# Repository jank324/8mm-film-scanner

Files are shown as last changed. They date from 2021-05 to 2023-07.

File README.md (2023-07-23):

# 8mm Film Scanner

The _8mm Film Scanner_ is a project to build a scanner for digitising 8mm motion picture film in both the _Regular 8_ and _Super 8_ gauges by converting an old projector with the help of a [Raspberry Pi](https://www.raspberrypi.org) single board computer.

In this repository, I have collected all my materials on this project, including source code, information on the hardware and software design, instructions for using the software, a rundown of my scanning and editing workflow and many more.

You might also want to check out my [post about this scanner over on the *Kinograph* fourms](https://forums.kinograph.cc/t/8mm-film-scanner-my-build/2574).



### Table of contents

- [Introduction](#introduction)
- [Detailed technical description](#detailed-technical-description)
  - [Hardware design](#hardware-design)
    - [Projector conversion](#projector-conversion)
    - [Camera](#camera)
    - [Electrical systems and wiring](#electrical-systems-and-wiring)
    - [Base plate and case](#base-plate-and-case)
  - [Software design](#software-design)
    - [Scanning operations](#scanning-operations)
    - [Dashboard and other user experience](#dashboard-and-other-user-experience)
  - [Scanning workflow](#scanning-workflow)
  - [Cost](#cost)
  - [Future features and fixes](#future-features-and-fixes)
- [Run the software on your own scanner](#run-the-software-on-your-own-scanner)
  - [Installation](#installation)
  - [How to use](#how-to-use)
- [Contributing](#contributing)
- [Acknowledgements](#acknowledgements)

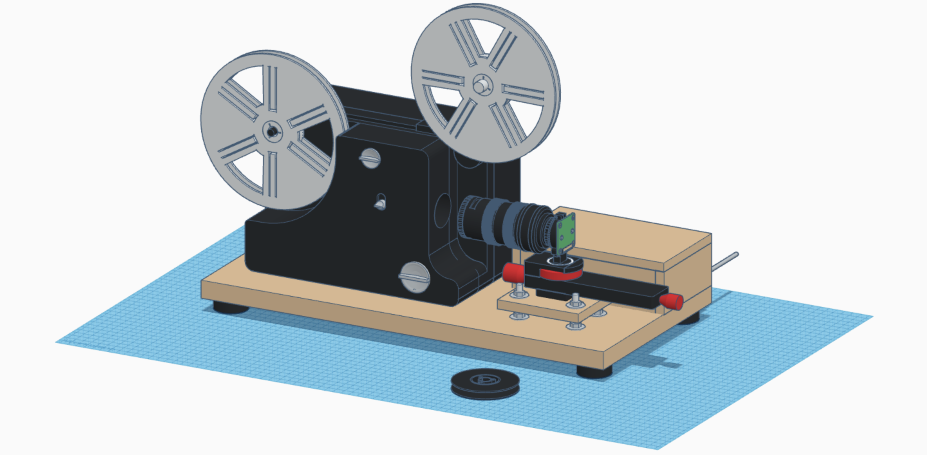
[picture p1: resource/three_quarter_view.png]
Three-quarter view render


## Introduction

I while ago, I found myself with over 800 rolls of 8mm film my grandfather had filmed throughout the 1960s, 70s and 80s. Having just digitised my grandparents' photo collection, naturally I wanted to know what was on these 8mm films and digitise them as well, so they would be safe from further deterioration and so we would actually watch them instead of always being too lazy to set up the projector.

The easiest way to get films like these digitised is the use of a digitisation service. But for the sheer amount of film I had, this would have cost me well over 10,000€ and with these services you never know whether you will actually receive a decent quality scan. The next option was to get out the old projector and use a video camera to record the films as they play. This is a perfectly valid option and super easy to do, but the resulting recordings usually suffer from image distortion, bad colours, a lack of sharpness and quite a bit of flicker. To do the true quality of these films justice, what was really needed was a frame-by-frame scanner that takes an image of every single frame of the film directly off of the film itself. You can actually buy these, but the ones available are either so expensive that they only make sense for professional users (e.g. scanners by [Filmfabriek](https://filmfabriek.nl)) or they leave a lot to be desired in terms of quality (like the famed [Wolverine](https://www.wolverinedata.com/products/MovieMaker_Pro)).

The solution is to build your own scanner, an idea that I got hooked on after finding a [video on the AACA Library's _Mike's Movie Machine_](https://www.youtube.com/watch?v=luGacxJMZI8), which is really just an incarnation of the absolutely amazing [_Kinograph_](https://www.kinograph.cc) project. The Kinograph project is accompanied by the [Kinograph forums](https://forums.kinograph.cc), quite possibly the best community on motion picture film scanning you will find on the internet, hosting invaluable information and some incredible projects built by talented and passionate people. On scanner build project in particular that I would like to point out as they key inspiration for this project is [the build by Scott Schiller](https://youtube.com/playlist?list=PLIACRGgedheWF4xr1zxiASZ1QqJUfloQ2), who also produced an awesome video series about his scanner and his scanning workflow.

In the following, you will find a detailed description of my _8mm Film Scanner_ as well as my scanning workflow, using a dual-gauge film projector and a [Raspberry Pi](https://www.raspberrypi.org) with a _HQ Camera_.

Some of the features of this scanner include:

- Dual gauge scanning of both _Regular 8_ and _Super 8_
- Up to 3K resolution (though 2K is recommended, 4K is possible with modifications)
- Scanning independent from a computer, allowing for unattended scans
- RAW scanning workflow
- Support for up two 120 m (400 feet) reels
- An easy-to-use web interface (with a mobile version as well as light and dark modes)
- Once-piece design that takes no time to set up or stow away

Below you find ...

- ... a photo of the scanner
  Photo of the scanner

- ... a screenshot of the scanner's web interface (light mode)
  Web interface in light mode

- ... a video of sample scans

  https://github.com/jank324/8mm-film-scanner/assets/17012833/1bc203a3-f0e7-4aa9-b80b-c313283cab2c

The rest of this README is intended as a documentation of every detail and lesson learned about my scanner. The goal here is to provide all the information and source code required to build another one.

## Detailed technical description

This section will go over technical details of the _8mm Film Scanner_. The goal is to document provide other (or even myself at some point in the future) with everything needed to rebuild the scanner without having to redo all the research I did.

### Hardware design

In this section, the hardware of the scanner is described. It will go over how the projector was converted to be a scanner, the camera sensor, lenses and mount, the electronics supplying power to and communication between the components as well as the base plate holding everything together.

#### Projector conversion

The scanner is built around a _Bolex 18-3 TC_ dual gauge film projector. There was no particular reason why I used this projector other than that I found a very cheap one sold as defective in the local ads. I never tested the electric components of the projector, but the film transport was in perfectly fine condition, which is all I cared about for this project.

There are some almost identical models to this one by Bolex and Eumig, including the Bolex 18-3 Duo, Eumig 610 D, Eumig 605 D, Eumig 614 D and Revue Lux 3003. So, if you would like to follow along with this build, the conversion should be almost the same for these models. Other projectors, however, will also be just fine and look fairly similar.

In order to convert the projector, I removed the power supply and the motor/fan assembly from the left side of the housing. In its place, I mounted an acrylic base plate to mount new components to. A photo of the baseplate with its components is shown below. For this particular projector, a tensioning arm for the main drive chain was originally mounted to the motor/fan assembly. This was simply remounted on the base plate. Furthermore, a [Nema 17 1.5 A 12 V stepper motor](https://www.amazon.de/gp/product/B07KZQ77VH/ref=ppx_yo_dt_b_search_asin_title?ie=UTF8&psc=1) was mounted using a right angle [mounting bracket](https://www.amazon.de/gp/product/B07CM3LZD1/ref=ppx_yo_dt_b_search_asin_title?ie=UTF8&psc=1) designed for NEMA 17 stepper motors. A pulley is mounted to the shaft of the stepper motor. This pulley should match the belt shape and size of the projector, but it is possible to get away with mixing v-belts and a pulley for round belts. I've chosen [this pulley](https://www.amazon.de/gp/product/B07C4R3PGV/ref=ppx_yo_dt_b_asin_title_o05_s00?ie=UTF8&psc=1). Pulley needs to be aligned with the pulley on the projector's main drive shaft (in my case also the aperture wheel). The stepper motor needs to be mounted at the same distance to the drive shaft pulley, such that it maintains the same tension on the drive belt as the original motor did. It might also make sense to replace the belt with a new one. These are readily available online by searching for the projector's name. In addition to the stepper motor assembly, a [KY-024 Hall effect sensor](https://www.amazon.de/gp/product/B089QK1CHR/ref=ppx_yo_dt_b_search_asin_title?ie=UTF8&psc=1) is mounted on the rear of the baseplate using a right-angle bracket. A small [5x1 mm Neodymium magnet](https://www.amazon.de/gp/product/B07T13H3R5/ref=ppx_yo_dt_b_search_asin_title?ie=UTF8&psc=1) is mounted to the core of the aperture wheel. The hall effect sensor and the magnet need to be lined up. They are used to detect that the scanner has advanced one frame. Parts of the electronics are also mounted to the base plate, either using double sided tape or screws as appropriate. They are further described in the [Electrical systems and wiring](#electrical-systems-and-wiring) section.

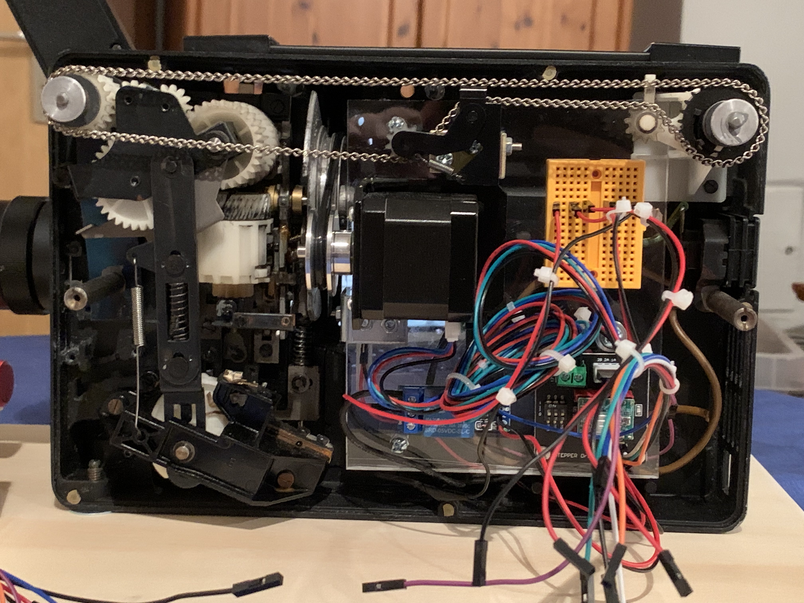
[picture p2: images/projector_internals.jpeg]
Projector internals


On the right side of the project, the original lens is remove. This allows the camera to take take photos of the film directly from the film gate. Furthermore, I removed a mask from the film gate in order to be able to capture a larger area of the original film frame. I did not drill out the film gate because I did not want to risk scratching the film, but this is certainly an option, if removing the mask does not reveal all of the frame. Neither removing the mask nor drilling out the gate is strictly required, but merely allows the scanner to capture more of the frame the would have been projected.

The original halogen bulb of the projector is replaced with an LED light bulb. Doing so is critical because the film and likely some of the components of the projector would overheat otherwise. Replacing the bulb with an LED very easy on this and many other models of projector, as MR16 LED bulbs can be mounted without any modifications. The bulb should be at least CRI 90+ and produce about 270 lm at an angle of 38°. I chose [this 3W bulb by _greenandco_](https://www.amazon.de/gp/product/B07F14F3N7/ref=ppx_yo_dt_b_search_asin_title?ie=UTF8&psc=1). Note that very similar 6.5 W _Philips Master expertcolor_ LED with with 420 lm turned out to be too bright in my earlier experiments. The colour temperature of the bulb should ideally be similar to the original halogen bulb, i.e. somewhere around 2700 K. In addition to mounting an LED bulb, the light of this bulb also needs to be further diffused. I used a 3mm sheet of white acrylic, specifically [_PLEXIGLAS LED white WH52 GT_](https://www.plexiglas.de/en/products/plexiglas/plexiglas-led). This specific type of acrylic by PLEXIGLAS is specifically designed to be colour-accurate for lighting applications and PLEXIGLAS themselves sell small samples for very little money. These samples are more than large enough (in fact I had to cut mine in half) for mounting in front of the MR16 bulb. Note the _WH52_ indicating the level of diffusion (and light attenutation) that work well with the LED bulb I chose. The acrylic is mounted to the front of the bulb mounting bracket using double sided tape as can be seen in the photo below.

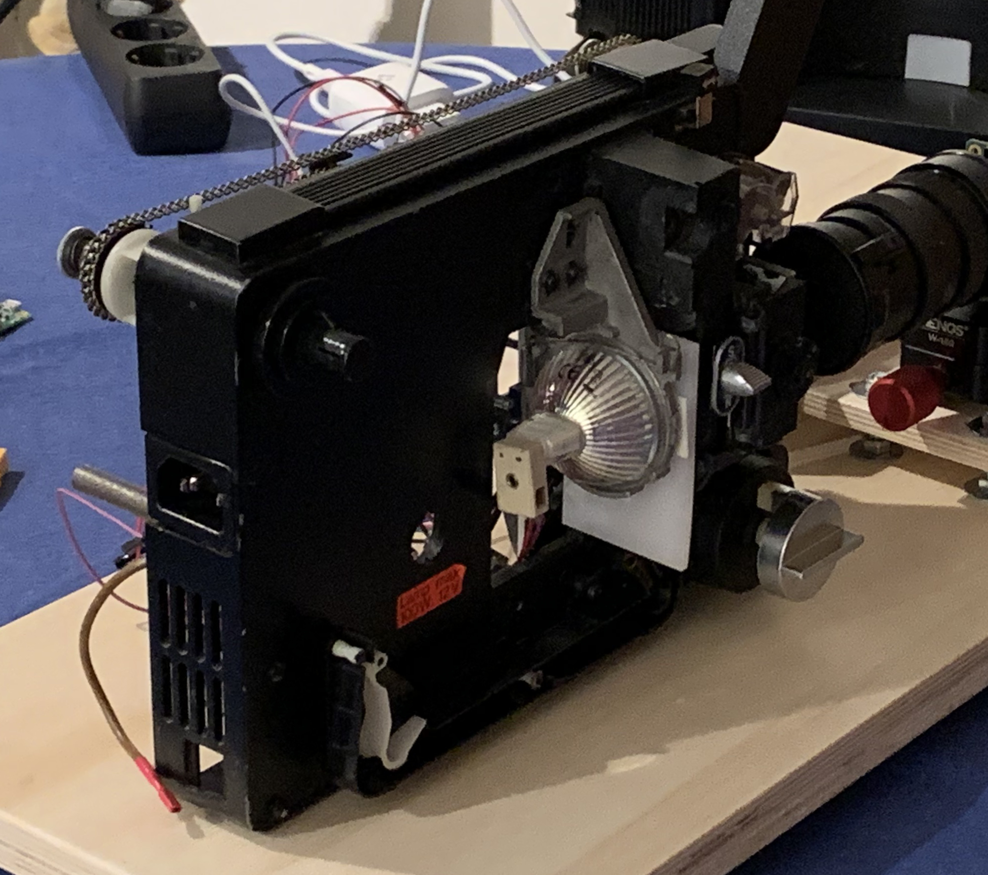
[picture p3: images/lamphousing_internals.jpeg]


#### Camera

The scanner uses the [_Raspberry Pi HQ Camera_](https://www.raspberrypi.com/products/raspberry-pi-high-quality-camera/) to capture the frames on the film. This model was chosen because it is easy to use with the Raspberry Pi, the image quality is more than adequate and the C-mount as well as its sensor size make it easy to adapt lenses and achieve the magnification required to have the small film frames fill the camera's image sensor.

The lens used is a _Schneider-Kreuznach Componon-S 50mm_ enlarger lens. Today, enlarger lenses are widely available on the used market. They well-suited to macro imaging applications and usually have a very flat image plane, helping us avoid focus vignetting. The Componon-S in particular is a very good quality model and a popular choice in the film scanning community, but other similar enlarger lenses are just as well suited.

The Componon-S has an M39 thread and therefore needs to be adapted to the camera's C-mount. It also needs to be mounted at some distance from the image sensor to achieve the enlargement required to make a Regular 8 or Super 8 frame fill the camera's sensor. As finding adapters directly from C-mount to M39 turned out to be rather difficult, I chose to adapt via M42-mount. This mount was widely used by Pentax in the 1960s and 70s, making adapters to other mounts as well as macro extension tubes very easy to find. The following components are used to adapt the enlarger lens to the HQ Camera (starting from the camera):

- C-mount to M42 adapter
- 19 mm M42 extension tube
- 26 mm M42 extension tube
- M42 to M39 adapter ring (screws into the inside of the M42 thread and is therefore not visible)

The picture below shows the final camera assembly. Note that the M42-to-M39 adapter is not visible as it screws into the inside of the extension tube's thread before the lens is screwed in.

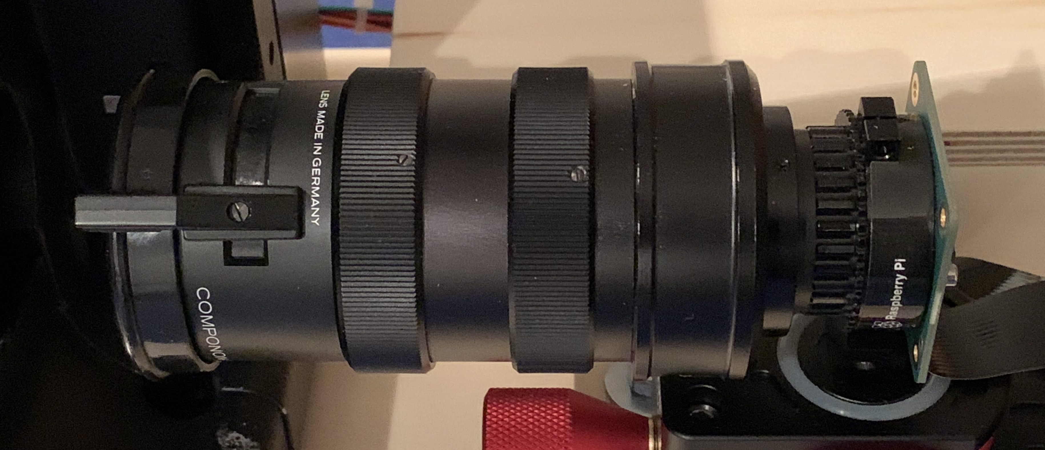
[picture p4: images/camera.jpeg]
Camera


Using the HQ Camera's tripod mount, the camera is mounted on a _MENGS W-160_ macro slider that can be used to adjust focus. The same macro slider can often be found under different brands. The macro slider itself is mounted to a wooden baseplate with a [3/8-16x1 screw with a hex head](https://www.amazon.de/gp/product/B07JGWWSFK/ref=ppx_yo_dt_b_search_asin_title?ie=UTF8&psc=1) that was shortened. Four M6x50mm screws with hex heads are used to mount the base plate to the main plate of the scanner. Using four pairs of nuts and washers, it is possible to adjust the height of the camera. The four wholes to mount the base plate are elongated in parallel to the film plane, allowing for horizontal adjustment of the camera position. More details and measurements of this camera mount can be found in the [Base plate and case](#base-plate-and-case) section.

The lens is always used at an aperture of f4.7. This was found to be the aperture at which the lens is by far the sharpest and lets in the correct amount of light for the rest of the camera setup.

The forward end of the lens is somewhere around 78 mm away from the film gate, but this has likely changed since as a result of focusing adjustments.

I have published [further studies on the camera setup on the Kinograph forums](https://forums.kinograph.cc/t/reverse-mounting-schneider-componon-s-50-mm-on-c-cs-mount/1767/8?u=jankaiser).

#### Electrical systems and wiring

Below you can see an overview of the scanner's electrical systems with red and black connections representing positive and negative power connections, and all other colours representing signal connections.

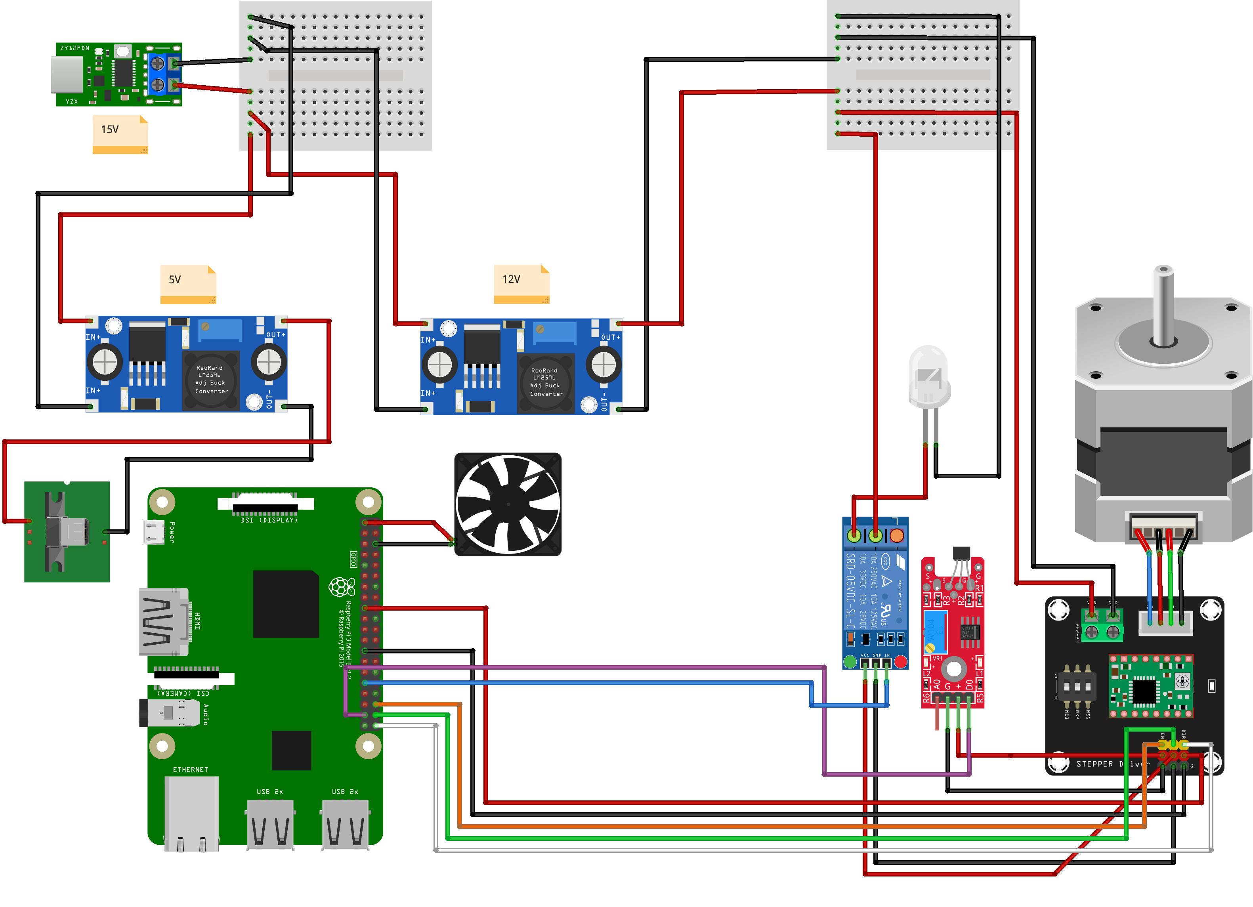
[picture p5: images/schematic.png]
Overview of electrical systems


The scanner is powered by a fairly standard [45W USB-C power supply](https://www.amazon.de/gp/product/B098P15D4N/ref=ppx_yo_dt_b_search_asin_title?ie=UTF8&psc=1). The power supply is connected via a USB-C cable with USB-C PD support to a [ZY12PDN USB-C PD trigger board](https://www.amazon.de/gp/product/B08FD6381L/ref=ppx_yo_dt_b_search_asin_title?ie=UTF8&psc=1). This board is capable of negotiating with the power supply that it should deliver power as well as the USB-C PD mode that is used. Different modes differ primarily in the delivered voltage. The trigger board can be configured via a button on the board to negotiate a particular voltage. In this particular case, the trigger board is configured to negotiate the 15V mode, though 20V would work just as well. Note that the power supply must support the mode. If the power supply does not support the mode the trigger board asks for, USB-C PD will fall back to 5V. At this voltage the scanner will not work, but 5V will not damage it either.

A pair of [LM2596S step down modules](https://www.amazon.de/gp/product/B07YWLCTLK/ref=ppx_yo_dt_b_search_asin_title?ie=UTF8&psc=1) are then used to step the 15V from the power supply down to 5V required by the Raspberry Pi and 12V for the stepper motor and the LED light. While it would be possible to connect the Pi to the step down converter directly using jumper wires on its GPIO pins, the Micro USB end of an old USB cable is used instead. This keeps the Pi's fuses in circuit and protects the Pi in case of a problem with the power supply.

The stepper motor is driven by an [A4988 stepper driver](https://www.amazon.de/gp/product/B07C2V9GWC/ref=ppx_yo_dt_b_search_asin_title?ie=UTF8&psc=1) that sits on a [very practical PCB](https://www.amazon.de/gp/product/B07RGJQFSX/ref=ppx_yo_dt_b_search_asin_title?ie=UTF8&psc=1) which makes it easier to mount and connect the driver. The Pi controls the stepper motor direction via its GPIO 21 pin (white), enables the stepper via its GPIO 16 pin (orange) and steps the motor via its GPIO 20 pin (green). Using the switches on the PCB, the driver is configured to run the stepper motor in full-step mode. Note that this PCB also has additional positive and ground supply pins which are used to make the Pi's 3.3V available in the projector housing due the the location of the Pi in the wooden case.

The LED light is controlled by the Pi using a KF-301 relay module that can switch the 12V supply to the light. The relay receives its logic power from the 3.3V supply of the Pi and is controlled via the Pi's GPIO 6 pin (blue). It is important that the relay is connected to the 3.3V supply and **NOT** the 5V supply, the the logic level is 3.3V and it will not trigger properly otherwise. The relay is connected to the LED light through through the original bulb's GU5.3 socket.

The hall effect sensor, too, is connected to the Pi's 3.3V rail through the stepper PCB. It's digital signal output is connected to the PI via the GPIO 26 pin (purple). A potentiometer on the hall effect sensor module allows for setting the threshold of the digital trigger. This setting will likely need adjusting to make the scanner work properly.

The Pi also supplies a small case fan from its 3.3V supply. The fan has proven critical in cooling the Pi inside its cases. A heatsink is also mounted on the Pi's SOC. All cooling components were purchased as part of a typical [Raspberry Pi cooling kit](https://www.amazon.de/gp/product/B07C2V9GWC/ref=ppx_yo_dt_b_search_asin_title?ie=UTF8&psc=1).

Two [mini breadboards](https://www.amazon.de/gp/product/B01M9CHKO4/ref=ppx_yo_dt_b_search_asin_title?ie=UTF8&psc=1) are used to help manage the wiring both inside the projector and the case containing the rest of the electronics.

#### Base plate and case

To make setting up the scanner and stowing it away as easy as possible, the entire system is mounted on a base plate. The base plate also provides housing for the electronics that did not fit into the projector's housing.

The entire base plate is built from 9 mm poplar plywood. For the main part of the base plate, two 9 mm sheets were glued together, giving the base a strength of 18 mm. The housing for the electronics is placed in the front left corner of the base plate. It is fully glued together. There are openings for the Raspberry Pi's ports and the power connector on its left side. A round hole on its rear side allows for wires to be passed through toward the projector housing. On the case's left side, three slits allow for cooling and a narrow slit is placed on the bottom for the camera's ribbon cable. The lid of the case is two sheets of plywood glued together, with the bottom sheet being smaller than the top one to allow the lid to sit firmly on the top of the case. For protection, all wooden parts of the base plate are painted using [edding 5200 semi gloss clear coat](https://www.edding-fachshop.de/edding-5200-Permanentspray-Klarlack-4-5200995-ar941.aspx), but other clear coats should do just fine. The image below provides dimensions for the base plate.

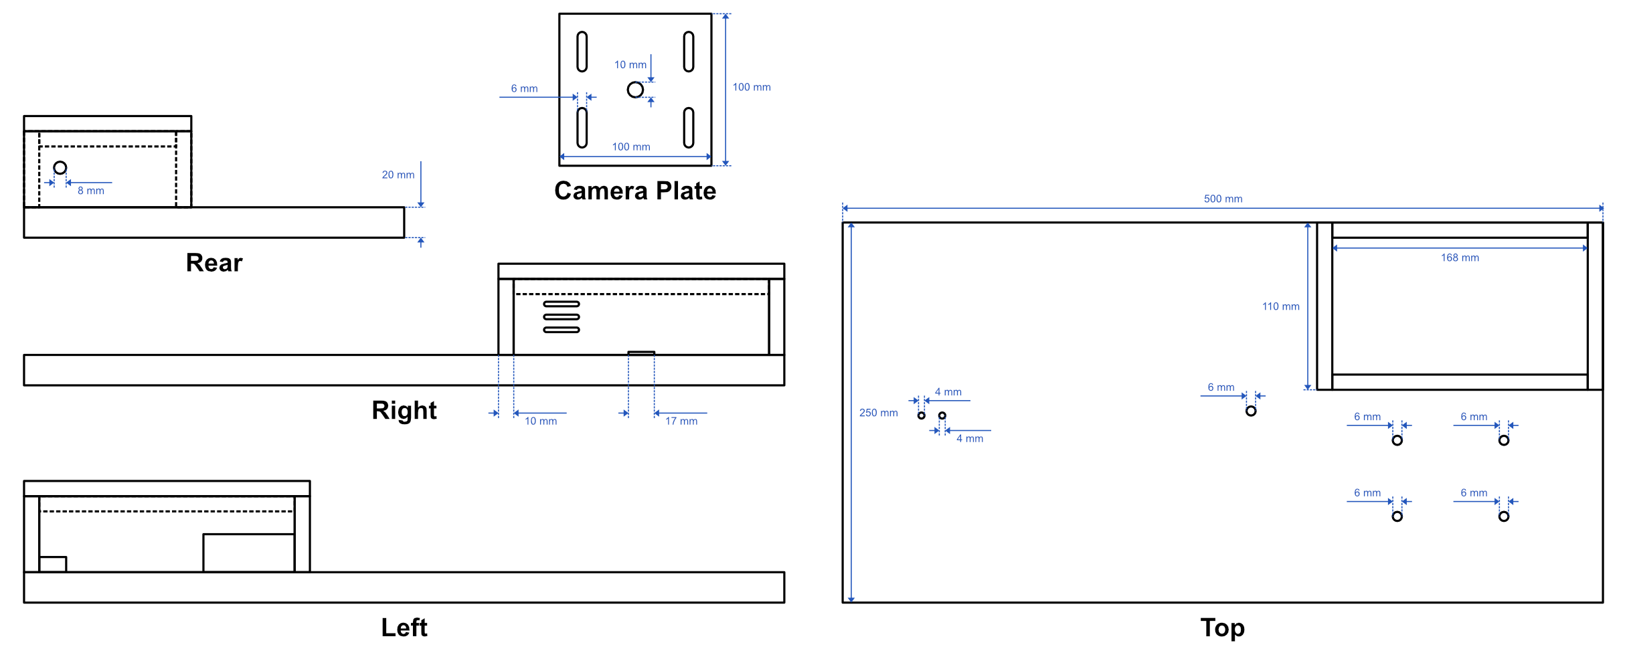
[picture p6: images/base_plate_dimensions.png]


Inside the electronics housing, all PCBs are mounted using double sided tape. The same applies to a small cooling fan mounted in the inside of the three cooling slits. This fan is strictly necessary to provide cooling to the Pi and the power supply components. I have found in tests, that with the fan and the cooling radiators installed on the Pi, the SOCs temperatures under load remain significantly lower than they do with the Pi out in the open air but without a cooling fan or radiator. The inside of the electronics housing is shown below.

Case internals

The projector is mounted using screws through holes. The screws are screwed through the base plate and into the holes that the projector's feet were originally screwed into. Note that this particular projector uses a special type of screw thread on the front that is 6mm in diameter and has two threads, each with twice the pitch of a standard M6 thread. I was unable to find buy a suitable screw for this, but the original foot is effectively a screw and worked just fine as such to mount the projector to the base plate. To mark the screw holes for the projector in the correct locations, a piece of paper was place on the bottom of the projector, the holes were traced and then transferred to the plywood. As the bottom of the projector is not at a perfect right angle relative to its sides and the film gate, washers were pushed under the higher side such that the projector stands mostly upright.

A camera mounting plate made from plywood is installed in the front left corner. It is further detailed in the [Camera](#camera) section.

### Software design

The software for this project consists of two parts: the film scanning logic taking care of film advance and image capture, and the user interface logic serving a web interface to simplify and streamline the interaction with the scanner.

#### Scanning operations

The scanning operations, including advancing the film and capturing frames, are handled by the `FilmScanner` class. Scanning is done by capturing the current frame, submitting it to a concurrent save method and then triggering the frame advance before repeating the process. To advance to the next frame, the stepper motor is ramped up and then run at a constant speed until the hall effect sensor was detected, at which point it is ramped down again. There is both a minimum time that has to pass before a completed frame advance may be detected as well as a timeout. If a timeout is detected before the hall effect sensor, the scanner will attempt to recover by reversing the advance mechanism until the hall effect sensor it detected and then reattempting the frame advance. Before submitting a frame for concurrent saving, the scanner might wait, if the previous frame has not finished saving yet. This prevents unsaved frames from piling up if the memory is slow for some reason.

The `pigpio` package is used to interface with the Hall effect sensor, the LED light and the stepper motor. The `picamerax` package is used to interface with the HQ camera.

The scanning code provides callbacks for various events, such as beginning and end of a scan, make it easy to implement various functions, e.g. the GUI or e-mail notifications, without the need to modify the actual scanning code.

#### Dashboard and other user experience

In order to make setting up and monitoring scans easier, the scanner provides a GUI. The goal was to make the scanner fully independent from other devices, such that a scan can be set up and then run fully unattended without even the need for a PC to be connected. To this end, a web interface was chosen. The web interface can be opened on any PC or even smartphone or tablet with a browser that is on the same network as the scanner, and it can be closed as soon as the scan is setup without interfering with the scan. Furthermore, the web interface can be reloaded at any time to check on the scan, again without interfering with the latter. Screenshots of both the desktop and mobile version of the web interface are shown below.

| Desktop web interface (dark mode) | Mobile web interface (dark mode) |
| :---: | :---: |
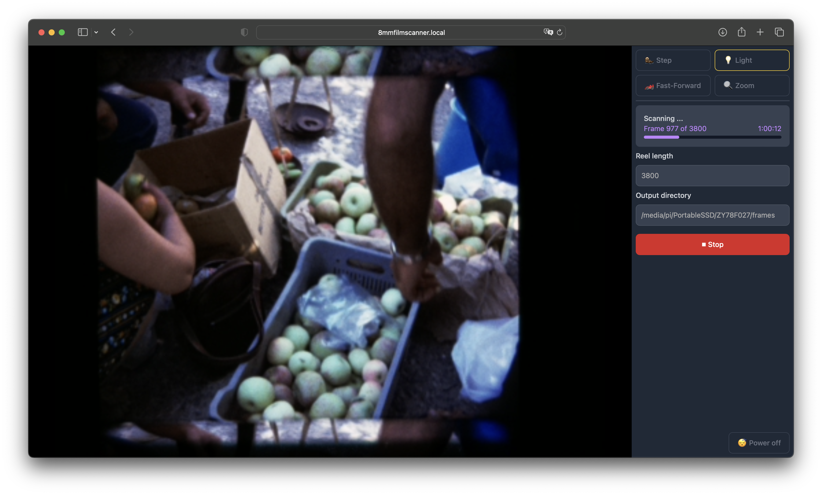
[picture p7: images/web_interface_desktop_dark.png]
Desktop web interface dark mode
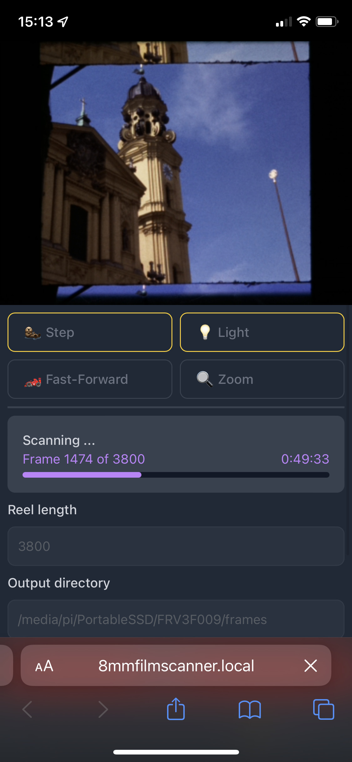
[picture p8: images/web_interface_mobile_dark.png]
Mobile web interface dark mode
|  |  |

The web interface is implemented in `server.py` using the _Flask_ package. A number of commands that can be sent to the scanner are implemented via different routes. The scanner also streams a live preview of the camera. During scanning, this preview is replaced with the most recently scanned frame.

The frontend of the web interface is implemented in Javascript as a [_React_](https://react.dev) app in the `frontend` directory. [_Tailwind CSS_](https://tailwindcss.com) was used for styling.

Automated e-mail notifications are implemented using a callback to the callbacks provided by the `FilmScanner` class. These are currently set up to send an e-mail notification when a scan has finished or was aborted because of some error. Note that this requires the scanner to have either its own e-mail account or access to the user's e-mail account.

### Scanning workflow

In this section I would like to briefly go over my current scanning workflow to illustrate how the scanner may be used to produce archivable digital copies of 8mm film reels. Note that this is what my workflow looks like right now and likely to change and evolve over time. It also certainly is not the only way to do it and there probably are better ways to get the results you are looking for.

Before starting to scan any of my film, I actually started by creating a list of all the film I have, giving every film a unique ID so I can identify them later. This allows me to easily track the progress of my scanning project over a long period of time and see which reels I have already scanning or what stage of post-processing I last left them in. Based on the IDs, I maintain a spreadsheet with various information on each reel. This includes their current status, which can be any one of _not digitised_, _old digitisation_, _in progress_, _scanned_ and _finalised_, where _old digitisation_ refers to a reel digitised with an inferior method many years ago and _finalised_ means that a reel has been into a larger film project (for example of all reels from a holiday). Further, the spreadsheet contains information on where to find the physical reel, the type of film, its length and what larger project the reel belongs to. In my particular case, many of the reels were actually labeled with detailed information on their contents. I have created a text document that with typed copies of these labels and the corresponding reel ID. A screenshot of the spreadsheet is shown below.

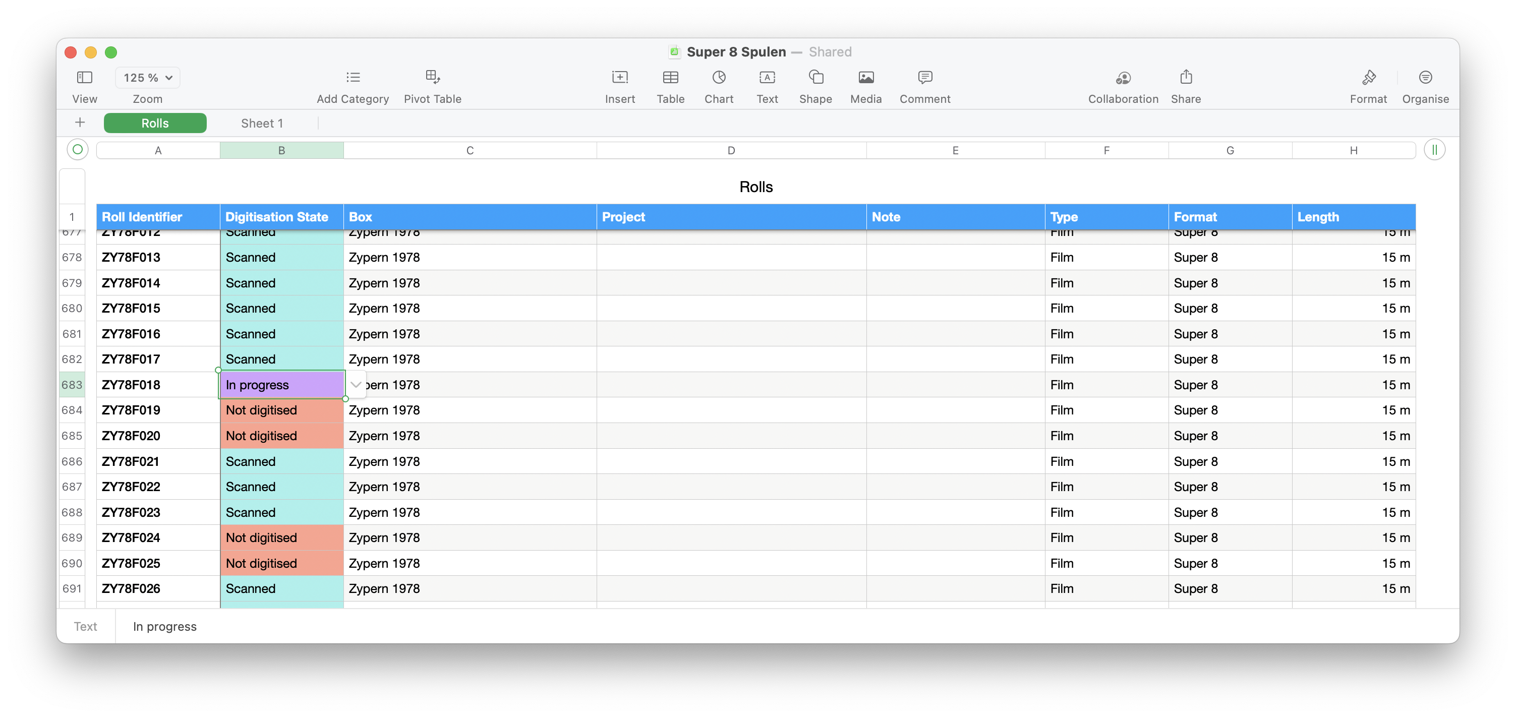
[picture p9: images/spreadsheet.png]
Spreadsheet


When it is time to scan a particular reel, I start by physically cleaning the film. To do this, I put the film on a film editing viewer. Then I put a few drops of [TETENAL Graphic Arts Film Cleaner](https://www.fotoimpex.com/darkroom/tetenal-graphic-arts-film-cleaner-1-liter.html) onto a lint-free cloth and spool the film onto another reel while grabbing the film with the soaked piece of cloth. It is advisable to swap the spot on the cloth every couple of meters and put on new cleaning solution as to avoid scratching the film with the dirt that came off it. Once the film is completely wound over, I wind it back onto its original reel. Note that I only attach the end of the film to the original reel very loosely so it comes off the reel easily when scanning. For your average Super 8 reel this is easiest done by not putting the film into the "claw" that is supposed to hold it, but to gently place it in the slit that usually allows you the see how full the reel is. Then just wind and the film will stay in place.

I then thread the film onto the scanner and fast-forward to the first frame that is fully visible. I use this frame to focus the camera onto the film grain. The _Zoom_ view offered by the web interface is very useful for the final focus adjustment. You might need to focus back and forth a little bit, until **the grain** appears as sharp as it gets.

For the number of frames to scan, I usually estimate the number of frames on the reel based on its length and the pitch of the film type, and then add ca. 5% to be sure to capture the entire film in one go. For example, for a 15 m (50 feet) reel, I capture 3800 frames, while the reel usually actually has around 3600 frames.

Rather than saving the scan on the Pi's SD card, I connect an external SSD via USB. It turns out this is significantly faster than using the SD card, so much so that with the SD card, the scan may be slowed down waiting for frames to save, which does not happen at all when using an external SSD. Note that I think for its speed, it is important to choose an SSD over a hard drive here. The path I select is `/media/pi/*path-to-ssd*/*rheel-id*/frames`.

Once the scan (or multiple scans) is done, I shut down the scanner and connect the SSD to my computer. At this stage I usually like to delete the empty frames from the end of the reel to save memory and processing time in the next steps. The Pi captures images, but only attaches the raw bayer data to JPG files. Therefore, the next step is to use the `dngconverter.py` script to convert the images to `.dng` files. Note that this specifically requires version `3.4.7` of the `pidng` package. The script provides a `--delete` option to automatically delete the original JPG files once they have been converted, but I prefer to do this manually once I know the conversion was successful. The converted DNG files may appear green. This is not a problem!

The next step is to import all the images into [_Adobe Lightroom_](https://lightroom.adobe.com). Here, we correct the white balance and the exposure, and crop into the frames, making sure to include the whole frame, not just a 4:3 crop of it. Some film stocks have changed colour or faded over time. They might required a colour correction as well. Luckily, the very common Kodachrome film stock usually retains its colours excellently. Use Lightroom's _Copy Develop Settings_ feature to make sure the settings are consistent for all frames on the reel (or at the very minimum the in the scene).

The `Super 8 Base (Kodachrome 1978).xmp` file provides a Lightroom preset that I always start from. It was tuned on unfaded Kodachrome stock that seems to have retained its colour just fine (it matches Kodak Ektachrome from 2022). This preset does three things: It matches the white balance to the light source, lifts the exposure to a be correct for a properly exposed film and reduces the contrast by lifting the shadows and lowering the highlights. The white balance was taken from a completely white and slightly underexposed photo of the film gate. Note that it does not perfectly match the advertised temperature of the LED, this is fine. The exposure is corrected in Lightroom instead of simply exposing one stop brighter in-camera to prevent highlights from blowing out. Pulling in the shadows and the highlights accounts for the naturally contrasty nature for positive film stocks and Kodachrome in particular.

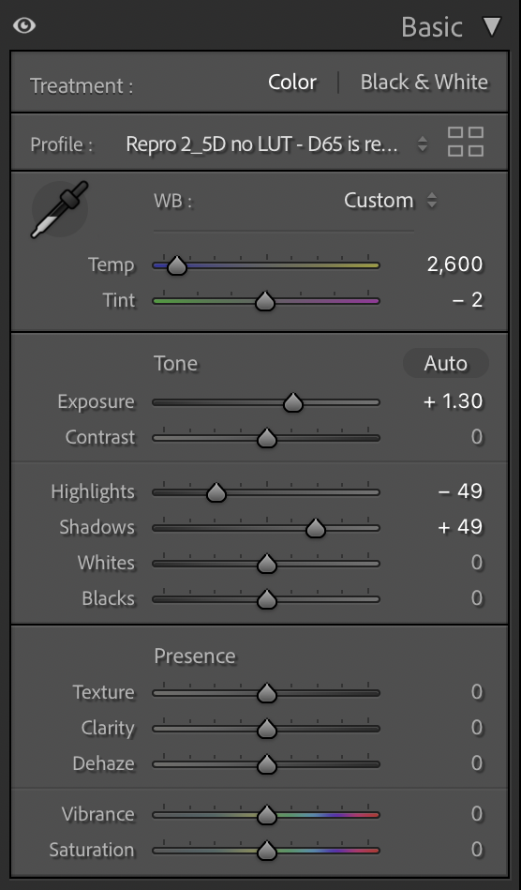
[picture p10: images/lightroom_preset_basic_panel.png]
Basic panel for the provided base Lightroom preset


While the provided exposure correction should be just fine for properly exposed scenes, you might encounter underexposed scenes in particular. Here it might make sense to pull up the _Exposure_ slider, but values of more than 2.9 usually don't reveal any more image details. Note that this is not a limitation of the image files, but of the film itself, as experiments with longer exposure times have shown. Next, the frames are exported as TIFF files. I choose 8 bit TIFFs, as the frames are already (mostly) exposure- and colour-corrected. I also turn off compression as these are only temporary files and doing so significantly reduces export times. I like to export to an `lr_export` directory right next to the original `frames` directory.

Once the export has finished, I use _Apple Compressor_ to render a video file from the exported images. Choose the little plus icon at the bottom of the Compressor window, click _Add Image Sequence_, select the `lr_export` directory with the exported frames in it and make sure to choose _Manually to_ with the correct frame rate for your film gauge (16 fps for Regular 8 and 18 fps for Super 8). I export to _Apple ProRes 422_ to retain quality in an intermediate format. In addition, I name my output file `*reel-id*_lr_export.mov` and save it in the same directory as the `frames` and `lr_export` directories.

At this point I check the exported video file, primarily because I'm excited to see the film for the first time, but also to check for issues that might warrant a second scan before I move on.

The next step is to fix defects and remove the gate weave from the footage in my video editing software. I use _Final Cut Pro_.

**Note:** While Final Cut doesn’t officially support 18 fps projects, with a little workaround it will handle custom frame rates easily:

1.  Create a new empty project make sure it already has the correct resolution and colour space set. You will not be able to change it later.
2.  With the project selected, go to _File_ → _Export XML…_ and save the `.xml` file somewhere.
3.  Open the `.xml` file and find all the `frameDuration` fields. Change them to match your desired frame rate in the format that they are currently in. A screenshot below shows an example changed to 16 fps below. Don’t forget to save the file.
4.  Now, go back into Final Cut. Select _File_ → _Import_ → _XML_ and select the `.xml` file.

You should now have a project that correctly shows that it is 16 fps (or whatever you selected). If you want to avoid having to redo this process all the time, you can simply duplicate the project when you need a new one.

**A little trick here:** Duplicating with the keyboard shortcut _cmd+D_ works even when the context menu item is greyed out. Only Apple know why 🤔.

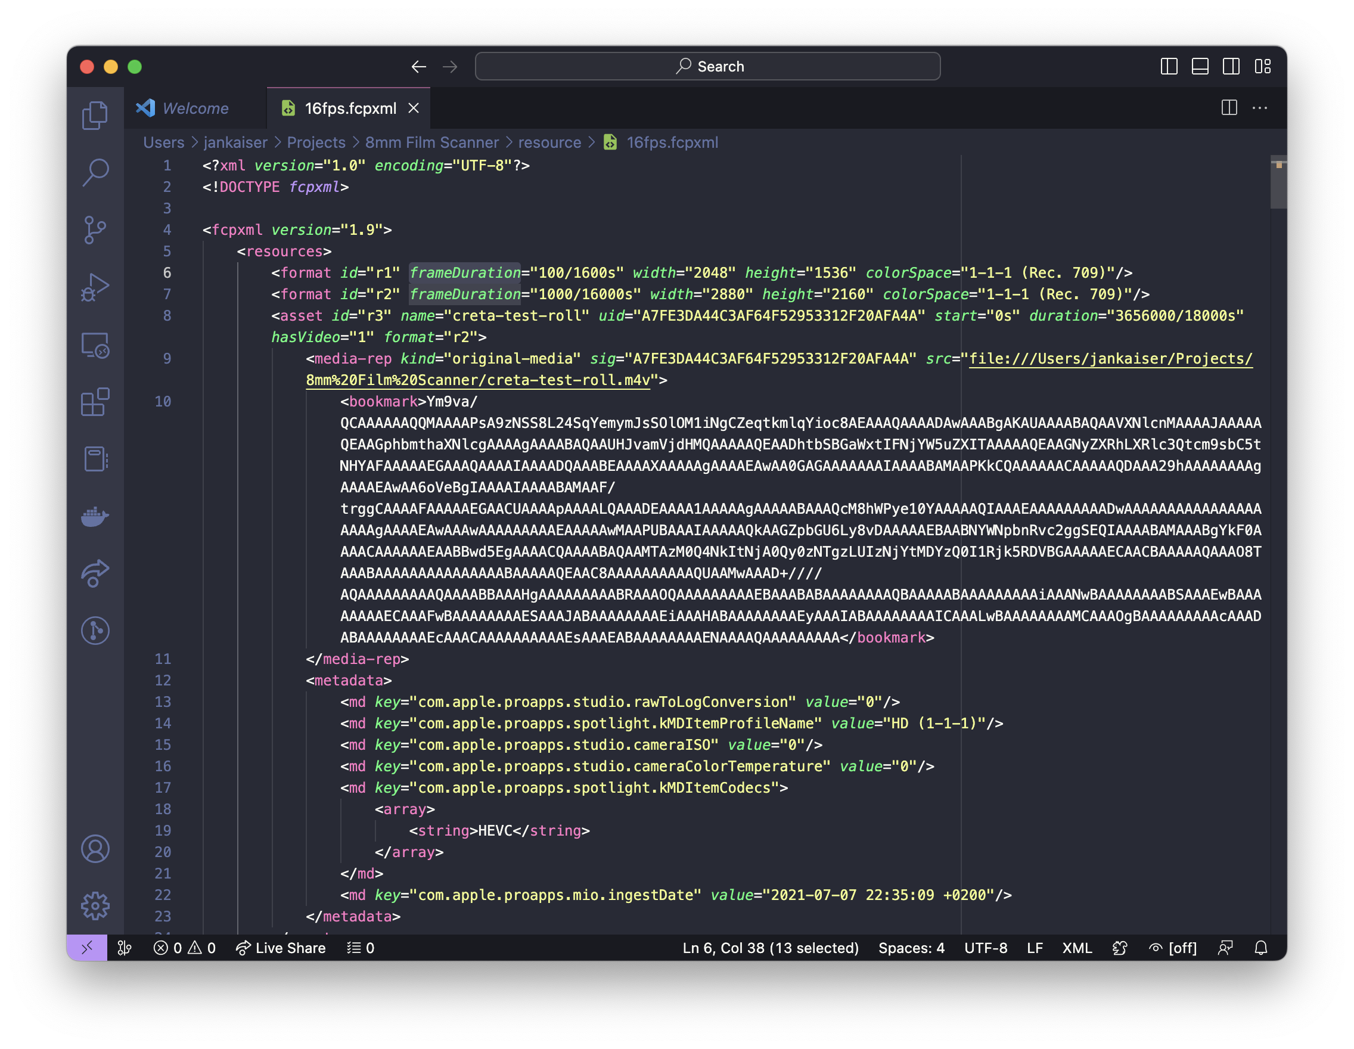
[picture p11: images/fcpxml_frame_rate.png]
Screenshot of a 16 fps .fcpxml file


After importing the clip, I first crop it to the correct aspect ratio by selecting _Spatial Conform_ -> _Type_ -> _Fit_ for the whole clip. Then I go through the clip from beginning to end and cut it at each scene change. Sometimes in analog film, frames between scene changes at overexposed or have light leaks. I like to remove these frames. I then stabilise each scene using the _SmoothCam_ method. To make sure I'm only removing the gate weave but retaining original camera movement as much as possible, I turn the _Rotation Smooth_ and _Scale Smooth_ settings all the way to 0.0. The _Translation Smooth_ setting is set to 0.33. Note that for any lower setting, Final Cut will not perform any stabilisation. In some scenes (for example when shot from a driving car) the natural shakiness of the footage overpowers the gate weave. In these cases, I will not stabilise the clip, because doing so would look over-processed and crop in too much into the original footage. Sometimes clips seems table, but Final Cut still chooses to crop in a lot. In these cases it might help to remove just a few frames from either end of the clip. This step of the process is also the right time to remove scenes with those from other scans of the same reel, if there were defects like black frames, doubled frames or large static pieces of dust in your scan.

Once all of this is done, I will export the clip to _Apple ProRes 422_ to `*reel-id* fixed and stabilised` and reimport it to Final Cut. This is done to reduce processing times in the next step.

For the next step, I create a new project in Final Cut and add two copies of the reel stacked on top of each other. I leave the top clip untouched and apply the [_Neat Video_](https://www.neatvideo.com) filter to the bottom one. In Neat Video, I deactivate the _Spatial Filter_. The _Temporal Filter_ is left activated and setup as shown below. These settings make sure to retain the grain but remove the dust. In an ideal world, I would just apply this filter to the entire clip. Unfortunately, this filter tends to produces quite unsightly artefacts from time to time. Therefore, I will go through the clip and deactivate sections of the unfiltered top clip only where there is a disturbing piece of dust, such that the bottom clip with the dust removed is visible for those frames. Sometimes is makes sense to only show part of a Neat Video frame, if there are artefacts in the rest of it. I find that the _Crop_ settings are usually the most convenient way to achieve this. My goal here is not to remove all the dust, but only to remove the dust that distracts from the viewing experience. Ideally the film would look like a very clean film would have looked in its day, not entirely free of dust, but not visibly dirty either. I achieve this by watching the film once, and removing all the dust that is clearly obvious. I then watch it again, preferably in full screen, and check if any such dust remains.

| Final Cut Pro setup for dust removal | Neat Video dust removal settings |
| :---: | :---: |
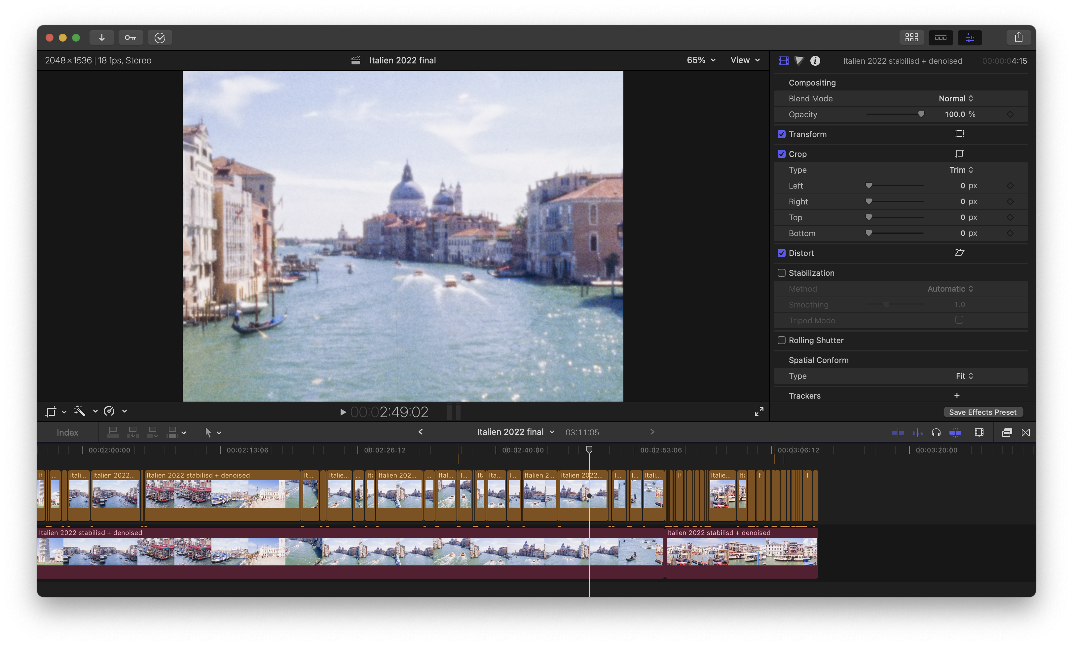
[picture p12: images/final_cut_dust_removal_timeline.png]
Final cut setup for dust removal
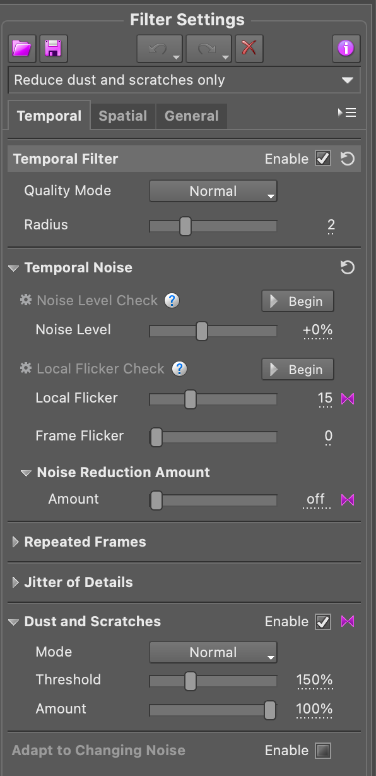
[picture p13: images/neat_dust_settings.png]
Neat Video dust removal settings
|  |  |

At last, I export the final clip as `*reel-id* final`. If the reel is part of a larger project, for example from a holiday, I will combine these final video files into a Final Cut project, once all reels have been scanned.

### Cost

Below is a table of all the items I used to build this scanner. Some of these I've already had, either because I bought them for an earlier project or because I was given them for some other reason. All prices are what I have actually paid or what I think they would have cost me if they were given to me. If I had to pay for shipping, this is included in the price. If I had to by multiple of the same item, even though I only needed one, I'm giving the price for the whole set. Your own milage may vary of course.

| Item | Price |
| :--- | ---: |
| Raspberry Pi 3B+ | 42.00€ |
| Micro SD card 32GB | 6.88€ |
| Jumper cables | 11.78€ |
| LED MR16 3W | 5.99€ |
| Relay | 3.99€ |
| Stepper Motor 1.5A | 10.99€ |
| Hall effect sensor KY-024 | 4.79€ |
| Neodymium magnets (100 pieces) | 6.99€ |
| A4988 stepper driver(s) | 7.49€ |
| Stepper driver parent PCB | 6.99€ |
| Stepper motor mount | 6.97€ |
| Belt pulley | 11.16€ |
| 50x25x6 mm acrylic sheet | 13.39€ |
| Raspberry Pi HQ camera | 59.78€ |
| Macro slider | 32.89€ |
| Screws | - |
| Bolex projector | 10.00€ |
| M42 to C-mount adapter | 39.90€ |
| M42 to M39 adapter | 7.26€ |
| Pentax extension tubes (3 pieces) | - |
| Schneider Componon-S 50mm enlarger lens | 64.99€ |
| 45W USB-C power supply (+ USB-C power cable) | 29.99€ |
| ZY12PDN USB-C PD trigger board | 12.99€ |
| Mini bread boards | 7.99€ |
| Poplar plywood 120x160x0.8 cm | 14.99€ |
| 38x15 mm rubber feet (4 pieces) | 4.99€ |
| 3/8-16x1 screw(s) | 6.99€ |
| PLEXIGLAS LED white WH52 GT sample | 3.00€ |
| Raspberry Pi cooling kit | 6.49€ |
| 50 cm Raspberry Pi camera ribbon cable | 7.99€ |
| Old micro USB cable | - |
| LM2596S step down modules (3 pieces) | 7.49€ |
| **Total** | **549.63€** |

### Current issues, future features and fixes

While the scanner has successfully scanned well over 50 reels over the past year already, there for remain a number of things that are not quite perfect just yet. I hope to fix these some day, but well all know that nothing survives as long as a temporary solution.

- **Dust removal workflow:** The dust removal as it is right now delivers excellent results, but it remains a lot of work. On a good day, I can currently finish the dust removal on one 15 m reel (just over 3 min) in 3-4 hours. At hundreds of reels to scan that is a very long time. Ideally, I would like a fully automatic solution. While Neat Video is great, letting it fully do a reel without supervision does not give satisfying results. In the future, I would like to explore a neural network-based solution, similar to already existing solutions for video restoration, but less heavy-handed.
- **Unreliable frame advance:** Most of the time the frame advance works just fine, but every 5k - 10k frames, it either produces a black frame, a doubled frame or a frame that is partially dark. This caused by the scanner not advancing fully, either because the Hall effect sensor was missed or because the belt connecting the stepper motor to the projector's mechanism slipped at the point where the mechanism has the most resistance. Unfortunately, because there is only this one sensor, the scanner cannot detect which of the two has happened (both have happened before, but now I suspect mostly the slipping). The problem is also difficult to debug due to it occurring so rarely, yet it happens often enough to be at least a little annoying. Possible solutions include:
  - Switching to a more reliable photo sensor. The Hall effect sensor seems to be not perfectly reliable due to its proximity to the stepper motor.
  - Adding a second sensor. This would allow the Pi to detect what has happened and recover it reliably if possible. To mount it, I would prefer to swap the base plate in the projector for a 3D-printed one that makes all components easier to mount.
  - Relubricating the projector's mechanisms. The projector's mechanisms may have more resistance than they should have. Adding new lubrication could fix this, but so far I have not dared to disassemble the mechanism to do this.
  - Ensuring proper belt tension on the drive belt. I have eyeballed the belt tension when installing the stepper motor, to be similar to the original motor. A slipping belt may be fixed by doing this properly. This is, however, outside of the scope of my personal expertise.
- **Crashing live preview:** Sometimes the live preview goes black or freezes. This is caused by the preview thread crashing. It is easily fixed by rebooting the scanner and therefore has not been annoying enough for me to fix yet. It, too, is difficult to debug as it only happens sporadically.
- **Lose PCB mounts:** All components in the Raspberry Pi case on the base plate are mounted using double sided tape. This is too lose, especially for the Pi and the USB-C PD trigger board, because they move a lot when plugging things in our pulling them out. The trigger board has actually come lose since I've mounted it. I would like to 3D-print a mounting rack that screws into the wood and holds all the components in the case firmly.
- **Web interface camera settings:** Adding camera settings to the web interface would be nice. I have not found the need for that yet, though, because all film stocks I have scanned so far worked with the same fixed exposure. This is actually to be expected with properly exposed films. Over- and underexposed films are easily fixed thanks to scanning in RAW format.

## Run the software on your own scanner

You are welcome to run this software or modified versions of it on your own scanner. A prerequisite is that the hardware is setup in roughly the same way (though it does not need to be based on a projector). You will need to make sure that the GPIO connections are either on the same pins as my scanner or that you change the code according to your connections.

These instructions may be incomplete. Furthermore, they have not been fully tested as I only have a single scanner. Please feel free to create an Issue for any questions you might have or problems you might find.

Start by cloning the repository (`Desktop`)

```sh
git clone https://github.com/jank324/8mm-film-scanner.git
```

and install the required Python packages.

```sh
sudo python3 -m pip install -r requirements.txt
```

Then install _npm_

`cd` to `frontend` directory.

```sh
cd frontend
```

and its required packages.

```sh
npm install
```

Continue to build the frontend via

```sh
npm run build
```

then `cd` back to the project root (`..`) where you can start the server by running

```sh
sudo python3 server.py
```

You probably want to run the server on boot of the Pi, so the scanner is ready to scan within seconds of you turning it on and without the need for you to start anything manually. To this end, this repository provides a _systemd_ service `8mmfilmscanner.service` that runs the 8mm Film Scanner's server on boot. To set up the service, copy the `.service` file to `/etc/systemd/system` by running

```bash
sudo cp 8mmfilmscanner.service /etc/systemd/system/
```

and then enable it via

```bash
systemctl enable 8mmfilmscanner
```

In order to send email notifications on finished scans, create a mail account of your choice or use your personal account. Create a file `notification_config.yaml` in the project root directory and fill in the following with the details of your mail account and the mail address you want e-mails to be sent to.

```yaml
user: scanners@mail.com # Address of the scanner's account
password: scanners-password-123 # Password of the scanner's account
to: your@mail.com # Address notifications are sent to (presumably your own)
```

Please remember to **NEVER** commit `notification_config.yaml` as it contains the password to the scanner's mail account which should remain secret. Under normal circumstances, this repository's `.gitignore` should already take care of this.

# Contributing

You are welcome to contribute to this project. If you find any issues, you may create a corresponding Issue here on GitHub. Even better, if you fixed something, you may create a Pull Request.

# Acknowledgements

First and foremost I would like to acknowledge Matthew Aepler and his [Kinograph forums](https://forums.kinograph.cc). The forums have been an invaluable resource for this project and are one of the best resources on motion picture film scanning out there. I would also like to acknowledge everyone who has contributed to the forums and thereby to this any many other projects. Furthermore, I would like to acknowledge [Scott Schiller and his scanner build](https://youtube.com/playlist?list=PLIACRGgedheWF4xr1zxiASZ1QqJUfloQ2), which have been a major inspiration for the direction of this scanner build project.

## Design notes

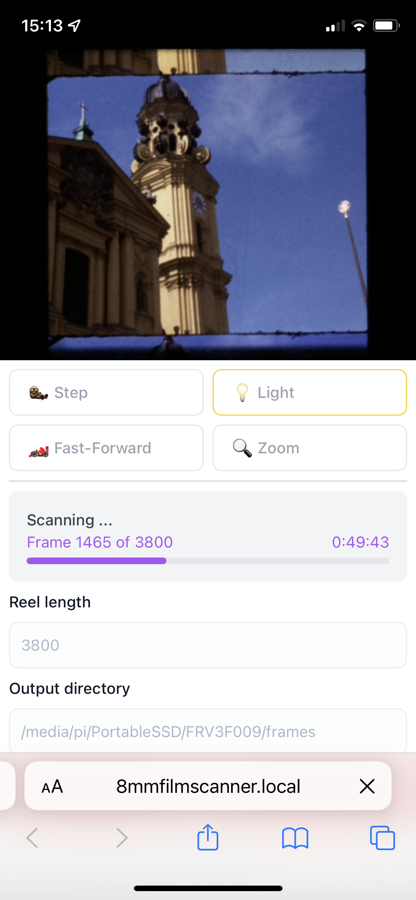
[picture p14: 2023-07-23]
images/web_interface_mobile_light.png

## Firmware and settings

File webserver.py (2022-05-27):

from flask import Flask, Response, request
from flask_cors import CORS

from filmscanner import FilmScanner
from notification import MailCallback
from utils import (
    AdvanceToggleCallback,
    FastForwardToggleCallback,
    LightToggleCallback,
    ScanControlsCallback,
    ZoomToggleCallback
)


app = Flask(__name__)
cors = CORS(app)

advance_toggle_callback = AdvanceToggleCallback()
fast_forward_toggle_callback = FastForwardToggleCallback()
light_toggle_callback = LightToggleCallback()
mail_callback = MailCallback()
scan_controls_callback = ScanControlsCallback()
zoom_toggle_callback = ZoomToggleCallback()

scanner = FilmScanner(
    callback=[
        advance_toggle_callback,
        light_toggle_callback,
        fast_forward_toggle_callback,
        mail_callback,
        scan_controls_callback,
        zoom_toggle_callback
    ]
)
scanner.camera.resolution = (800, 600)


@app.route("/advance", methods=("GET","POST"))
def advance():
    if request.method == "GET":
        return {
            "is_active": scanner.is_advancing and not (scanner.is_fast_forwarding or scanner.is_scanning),
            "is_enabled": not any([
                scanner.is_advancing,
                scanner.is_fast_forwarding,
                scanner.is_scanning
            ])
        }
    elif request.method == "POST":
        scanner.advance()
        return "", 204
    return "", 400


@app.route("/advance-stream")
def advance_stream():
    return Response(advance_toggle_callback.subscribe_to_sse(), mimetype="text/event-stream")


@app.route("/dismiss", methods=("POST",))
def dismiss():
    scanner.last_scan_end_info = "dismissed"
    return "", 204


@app.route("/fastforward", methods=("GET","POST"))
def fast_forward():
    if request.method == "GET":
        return {
            "is_active": scanner.is_fast_forwarding,
            "is_enabled": not (scanner.is_advancing or scanner.is_scanning)
        }
    elif request.method == "POST":
        if not scanner.is_fast_forwarding:
            scanner.fast_forward()
        else:
            scanner.scan_stop_requested = True
        return "", 204
    return "", 400


@app.route("/fastforward-stream")
def fast_forward_stream():
    return Response(fast_forward_toggle_callback.subscribe_to_sse(), mimetype="text/event-stream")


@app.route("/focuszoom", methods=("GET","POST"))
def toggle_focus_zoom():
    if request.method == "GET":
        return {
            "is_active": scanner.is_zoomed,
            "is_enabled": not scanner.is_scanning
        }
    elif request.method == "POST":
        scanner.live_view_zoom_toggle_requested = True
        return "", 204
    return "", 400


@app.route("/focuszoom-stream")
def focuszoom_stream():
    return Response(zoom_toggle_callback.subscribe_to_sse(), mimetype="text/event-stream")


@app.route("/light", methods=("GET","POST"))
def toggle_light():
    if request.method == "GET":
        return {
            "is_active": scanner.is_light_on,
            "is_enabled": not scanner.is_scanning
        }
    elif request.method == "POST":
        if not scanner.is_scanning:
            scanner.toggle_light()
        return "", 204
    return "", 400


@app.route("/light-stream")
def light_stream():
    return Response(light_toggle_callback.subscribe_to_sse(), mimetype="text/event-stream")


@app.route("/poweroff", methods=("POST",))
def poweroff():
    scanner.poweroff()
    return "", 204


@app.route("/preview")
def preview():
    def generate():
        for frame in scanner.preview():
            yield b"--frame\r\n" + b"ContentType: image/jpeg\r\n\r\n" + frame + b"\r\n\r\n" 
    return app.response_class(generate(), mimetype="multipart/x-mixed-replace; boundry=frame")


@app.route("/scan", methods=("GET","POST"))
def scan():
    if request.method == "GET":
        return {
            "is_scanning": scanner.is_scanning,
            "output_directory": scanner.output_directory,
            "n_frames": scanner.n_frames,
            "current_frame_index": scanner.current_frame_index if scanner.is_scanning else 0,
            "last_scan_end_info": scanner.last_scan_end_info,
            "time_remaining": scan_controls_callback.str_time_remaining
        }
    elif request.method == "POST":
        if not scanner.is_scanning:
            scanner.start_scan(
                output_directory=request.get_json()["output_directory"],
                n_frames=int(request.get_json()["n_frames"])
            )
        else:
            scanner.stop_scan()
        return "", 204
    return "", 400


@app.route("/scan-stream")
def scan_stream():
    return Response(scan_controls_callback.subscribe_to_sse(), mimetype="text/event-stream")


if __name__ == "__main__":
    app.run(host="0.0.0.0", debug=False)

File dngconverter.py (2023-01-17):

import argparse
from concurrent.futures import ProcessPoolExecutor, as_completed
from pathlib import Path

from pidng.core import RPICAM2DNG
from tqdm import tqdm


def bayerjpg2dng(jpg_path: Path, delete: bool = False) -> None:
    """
    Convert a the file at `jpg_path` to a `.dng` file. Deletes the old file if `delete`
    is set to `True`.
    """
    d = RPICAM2DNG()
    d.convert(str(jpg_path))

    dng_path = jpg_path.with_suffix(".dng")
    validate_file(dng_path, min_bytes=int(1e6))

    if delete:
        jpg_path.unlink()


def validate_file(path: Path, min_bytes: int = 1) -> None:
    """Check if file exists and has a file size larger than `min_bytes`."""
    is_valid = path.is_file() and path.stat().st_size > min_bytes
    if not is_valid:
        raise InvalidFileException(path)


class InvalidFileException(Exception):
    """Exception raised when a file was found to be invalid."""

    def __init__(self, filepath: Path) -> None:
        super().__init__(f'File "{filepath}" is invalid.')


def parse_arguments() -> argparse.Namespace:
    """
    Parse command line arguments to the Pi to DNG conversion utility. Returns the `args`
    object.
    """
    parser = argparse.ArgumentParser(
        description="Convert Raspberry Pi Bayer JPEGs to DNGs."
    )
    parser.add_argument("directory", help="Directory with the JPEG files")
    parser.add_argument("--delete", action="store_true")
    return parser.parse_args()


def main() -> None:
    args = parse_arguments()

    directory = Path(args.directory)
    filepaths = list(directory.glob("frame-*.jpg"))

    with tqdm(total=len(filepaths)) as pbar:
        executor = ProcessPoolExecutor(max_workers=2)
        futures = [
            executor.submit(bayerjpg2dng, path, delete=args.delete)
            for path in filepaths
        ]
        for future in as_completed(futures):
            _ = future.result()
            pbar.update()


if __name__ == "__main__":
    main()

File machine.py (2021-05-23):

from threading import Event, Thread
from time import sleep

import cv2
from imutils.video.pivideostream import PiVideoStream
from io import BytesIO
import numpy as np
from picamera import PiCamera
import RPi.GPIO as GPIO


class HallEffectSensor:

    def __init__(self, input_pin):
        self.input_pin = input_pin
        
        GPIO.setup(self.input_pin, GPIO.IN)
        GPIO.add_event_detect(self.input_pin, GPIO.RISING, callback=self.detect)

        self.reset()

    def detect(self, channel):
        self.has_detected = True
    
    def reset(self):
        self.has_detected = False


class Light:
    
    def __init__(self, switch_pin):
        self.switch_pin = switch_pin

        GPIO.setup(switch_pin, GPIO.OUT, initial=GPIO.LOW)

        self.is_on = False
    
    def turn_on(self):
        GPIO.output(self.switch_pin, GPIO.HIGH)
        self.is_on = True
    
    def turn_off(self):
        GPIO.output(self.switch_pin, GPIO.LOW)
        self.is_on = False


class StepperMotor:

    min_speed = 0.001
    max_speed = 0.0006

    def __init__(self, enable_pin, direction_pin, step_pin):
        self.enable_pin = enable_pin
        self.direction_pin = direction_pin
        self.step_pin = step_pin

        GPIO.setup(self.enable_pin, GPIO.OUT, initial=GPIO.HIGH)
        GPIO.setup(self.direction_pin, GPIO.OUT, initial=GPIO.LOW)
        GPIO.setup(self.step_pin, GPIO.OUT, initial=GPIO.LOW)

        self.enabled = False

        # Set motor direction counter-clockwise
        GPIO.output(self.direction_pin, GPIO.LOW)
    
    def enable(self):
        GPIO.output(self.enable_pin, GPIO.LOW)
        self.enabled = True
    
    def disable(self):
        GPIO.output(self.enable_pin, GPIO.LOW)
        self.enabled = False
    
    def accelerate(self, steps=10):
        for delay in np.linspace(self.min_speed, self.max_speed, steps):
            self.step(delay=delay)
    
    def step(self, delay=0.0009):
        GPIO.output(self.step_pin, GPIO.HIGH)
        sleep(self.max_speed)
        GPIO.output(self.step_pin, GPIO.LOW)
        sleep(self.max_speed)
        
    def decelerate(self, steps=10):
        for delay in np.linspace(self.max_speed, self.min_speed, steps):
            self.step(delay=delay)


class LiveView:

    def __init__(self):
        self.current_frame = None
        self.close_requested = False

        self.capture_thread = Thread(target=self.run)
        self.pause_event = Event()
        self.frame_event = Event()

        self.pause_event.set()
        self.capture_thread.start()
    
    def __del__(self):
        self.capture_thread.join()
    
    def close(self):
        self.close_requested = True
    
    def pause(self):
        self.pause_event.clear()

    def resume(self):
        self.pause_event.set()
    
    def run(self):
        camera = PiCamera()
        stream = BytesIO()

        for _ in camera.capture_continuous(stream, "jpeg", use_video_port=True):
            stream.truncate()
            stream.seek(0)
            self.set_frame(stream.read())

            stream.seek(0)

            if self.close_requested:
                break
            
            self.pause_event.wait()
        
        camera.close()
    
    def set_frame(self, frame):
        self.current_frame = frame
        self.frame_event.set()
    
    def get_frame(self):
        self.frame_event.wait()
        self.frame_event.clear()
        return self.current_frame


class FilmScanner:

    def __init__(self):
        self.mode = "liveview"  # TODO: Alternative would be "scan"
        self.counter = 0

        GPIO.setmode(GPIO.BCM)
        self.backlight = Light(6)
        self.motor = StepperMotor(16, 21, 20)
        self.frame_sensor = HallEffectSensor(26)

        # self.camera = LiveView()

        self.close_requested = False

    def __del__(self):
        self.motor.disable()
        self.backlight.turn_off()
        # self.camera.close()
        
        GPIO.cleanup()

    def advance(self):
        self.motor.enable()

        self.motor.accelerate()

        for _ in range(200):
            self.motor.step()
        self.frame_sensor.reset()
        
        while not self.frame_sensor.has_detected:
            self.motor.step()
        
        self.motor.decelerate()

        self.motor.disable()

        self.counter += 1

    def run(self, capture=False):
        # self.backlight.turn_on()
        sleep(1)
        self.motor.enable()

        # Run motor unless interupted
        i = 0
        photo_index = 249
        leaving = True
        while True:
            if self.frame_sensor.has_detected and not leaving:
                self.motor.decelerate()
                print(f"Taking photo {photo_index} at {i}")
                if capture:
                    self.camera.capture(f"testrun/img{photo_index:05}.jpg")
                else:
                    sleep(0.7)
                photo_index += 1
                i = 0
                leaving = True

                if self.close_requested:
                    self.motor.disable()
                    self.backlight.turn_off()
                    break
                else:
                    self.motor.accelerate()
            
            if leaving and i > 200:
                leaving = False
                self.frame_sensor.has_detected = False

            self.motor.step()
            i += 1

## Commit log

2021-04-11 Cleaned up repository
    [Sproket_8mm_001.obj, Sproket_super8mm_001.obj]
2021-04-12 Tested stepper motor with projector mechanism
2021-04-14 Ran tests with new stepper board
2021-04-14 Added enable line and moved to 3.3V
    [schematic.fzz]
2021-04-22 Tested Hall effect sensor
2021-04-22 Proof-of-concept for stepper control via the hall effect sensor
2021-04-22 Updated schematic with hall effect sensor
    [schematic.fzz]
2021-04-27 Adjusted stopping script to stepper driver board setup
2021-04-29 Install hall effect sensor and magnet properly
2021-04-29 I don't remember what I changed
    [schematic.fzz]
2021-05-05 Implemented class for stepper motor
2021-05-05 Implemented class for hall effect sensor
2021-05-15 Added relay for 12v circuit
2021-05-15 Utility scripts for turning LED on and off
2021-05-15 Another test run with camera
2021-05-16 Installed new stepper motor
2021-05-16 Added abstraction for 12v circuit
2021-05-16 Automated load and circuit connection
2021-05-16 Changed relay to only switch lamp
2021-05-17 Show (still) picture from the camera
2021-05-17 Played around with some buttons (but lamp does not work)
    [server.py]
2021-05-18 Updated schematic
    [schematic.fzz]
2021-05-18 Added advance button functionality
2021-05-18 Refactored hall effect sensor
2021-05-19 Implemented frame update on advance
2021-05-20 Added liveview with smooth frame advance
2021-05-21 Limited transmission framerate to available one
2021-05-22 Switched to more CLI and VNC type user interface
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2021-05-24 Switched to dark design
2021-05-29 Implemented new camera control panel
2021-05-29 Switched camera controls to grid layout
2021-05-29 Fixed camera setting labels
2021-05-29 Implemented conversion script for Pi Camera RAWs
2021-05-29 Added test capture button
2021-05-30 Added delay before taking picture to avoid shake
    [filmscanner.py]
2021-05-30 Moved video thread to live view
2021-08-05 Test software PWM (faster but no more reliable)
2021-08-07 Switched to pigpio with hybrid PWM
2021-09-10 Got advance working reliably for two runs (increase hall sensitivity)
2021-09-10 Did some comment calculation for correct wave timing in acceleration
    [filmscanner.py]
2021-09-10 Give stepper speed in steps per second
2021-09-10 Converted stepper controls to RPM
2021-09-10 Cleaned up stepper motor class
2021-09-11 Cleaned up Hall effect sensor class
2021-09-11 Fixed error when message when scan finsihed
    [filmscanner.py]
2021-09-11 Introduced custom error class
    [filmscanner.py]
2021-09-11 Moved sensor not reached exception handling
2021-09-11 Fixed frame advance bug in focus app
    [filmscanner.py]
2021-09-12 Initial flat-field correction tests on old frames
2021-09-12 Rudimentary script for fixing numbering issues in recorded frame names
2021-09-13 Copied flat-field frame once for each frame
2021-09-18 Added camera footage to image server
2021-09-18 Fixed image to byte on server and started remote scanner class
    [server.py]
2021-09-24 Tested framerate of live view stream
2021-10-10 Moved send and receive to different threads
2021-10-10 Fixed untidy close and frame freezing
    [server.py]
2021-10-16 Tested camera speed vs. stream speed
2021-10-16 Fixed live view stream to be smooth
    [webserver.py]
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2021-10-21 Fixed focus zoom black image
    [filmscanner.py]
2021-10-23 Refactored frame sensor and advance code
2021-10-24 Built prototype for RGB histogram
2021-10-31 Revert "Measured capture times"
    This reverts commit da16ca9f745deba0b407f48702f9af0eca1468b3.
    [filmscanner.py]
2021-11-07 Fixed black jpegs because of exposure mode off
    [filmscanner.py]
2021-11-10 Tested linear FFC on real frame (bad result)
2021-11-14 Refactored feature extraction and sample creation into function
2021-11-27 Switch to retained buffer
2021-12-04 Implement pulley slip recovery
    [filmscanner.py]
2021-12-20 Fixed relay model
    [schematic.fzz]
2021-12-27 Made Fritzing plan for electronics upgrade
    [schematic_upgrade.fzz]
2021-12-29 Fixed relay switching light
    [filmscanner.py]
2021-12-29 Add light relay switch fix
    [schematic.fzz]
2021-12-29 Add correct stepper driver board
    [schematic.fzz]
2021-12-29 Cleaned up schematic
    [schematic_upgrade.fzz]
2022-01-06 Fixed wire color to real-world truth
    [schematic_upgrade.fzz]
2022-01-07 Added power switch
    [schematic_upgrade.fzz]
2022-02-23 Schematic before seperation of projector and wood case
    [schematic_upgrade.fzz]
2022-03-15 Schematic with projector and wooden box separated
    [schematic_upgrade.fzz]
2022-03-16 Schematics for different relais locations
    [schematic_upgrade.fzz, schematic_upgrade_copy.fzz]
2022-03-16 Just to "save" different wire colour scheme schematic
    [schematic_upgrade_othercolor.fzz]
2022-03-16 Removed all but ultimately implemented wiring plan
    [schematic.fzz, schematic_upgrade.fzz, schematic_upgrade_copy.fzz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]
2022-03-19 Stress tested new case for heat dissipation
2022-03-20 Old measurements for frame sensor adjustment
2022-03-25 Investigated weird effects on new case
2022-03-25 Some cleanup after putting scanner into case
2022-04-18 Working version after case installation
2022-04-18 Removed debugging code from new case install
2022-04-23 Backend for new buttons
2022-04-23 Built new buttons (including tailwind)
2022-04-28 Introduce callbacks to backend (button states)
2022-04-28 Frontend listen to callback button state changes
2022-04-29 Fix on load toggle states in backend
    [webserver.py]
2022-05-07 Fix enabled return on loading web interface
    [webserver.py]
2022-05-07 Fix button disable
2022-05-14 Refactored frame capture and saving
2022-05-14 Fix light toggle not reacting when scan is started
    [filmscanner.py, utils.py, webserver.py]
2022-05-14 Fixed issue with logger writing old log files
    [filmscanner.py]
2022-05-15 Backend reports frame number to control panel
2022-05-15 Fix light button remaining disabled after scan
    [utils.py]
2022-05-22 Before switching from square control buttons to non-square ones
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2022-05-22 New toggle button style
2022-05-22 New and improved scan button
2022-05-22 Redesigned and repositioned power off button
2022-05-22 Fix scan button height
2022-05-22 Disabled look for control toggles and power off button
2022-05-24 Bugfix is /dismiss and dummy in /poweroff
    [webserver.py]
2022-05-24 Clean up props passing signature
2022-05-25 Fix not advancing during scan
    [filmscanner.py]
2022-05-25 Add modal to power off confirmation
2022-05-27 Working power off on backend
2022-05-27 Sensible defaults for output directory and number of frames
2022-05-27 Cut raw bayer data from during-scan preview images
2022-05-27 Fix light turning off at beginning of scan
    [filmscanner.py]
2022-05-28 Fix video feed not displaying in browsers other than Safari
    [server.py]
2022-06-01 Switched icon to SVG
2022-06-01 Add schematic to README
    [schematic.fzz]
2022-06-01 Switch schematic to png
2022-06-01 Fix schematic in README
2022-06-01 Addition on case fan
2022-06-01 Test example sample video in README
2022-06-04 Wrote on camera and some other stuff
2022-06-07 Vertically flip camera preview image
    [filmscanner.py]
2022-07-23 Improvements to Camera section
2022-12-27 CAD file for Raspberry Pi
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2022-12-27 Fix variable name in docstring
    [dngconverter.py]
2023-01-17 Fix DNG converter not deleting
    [dngconverter.py]
2023-05-28 Complete introduction (exept sample video)
2023-05-28 Finish camera setup section
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2023-06-04 Add screenshot of Final Cut setup for dust removal
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2023-07-23 Fix sample video
